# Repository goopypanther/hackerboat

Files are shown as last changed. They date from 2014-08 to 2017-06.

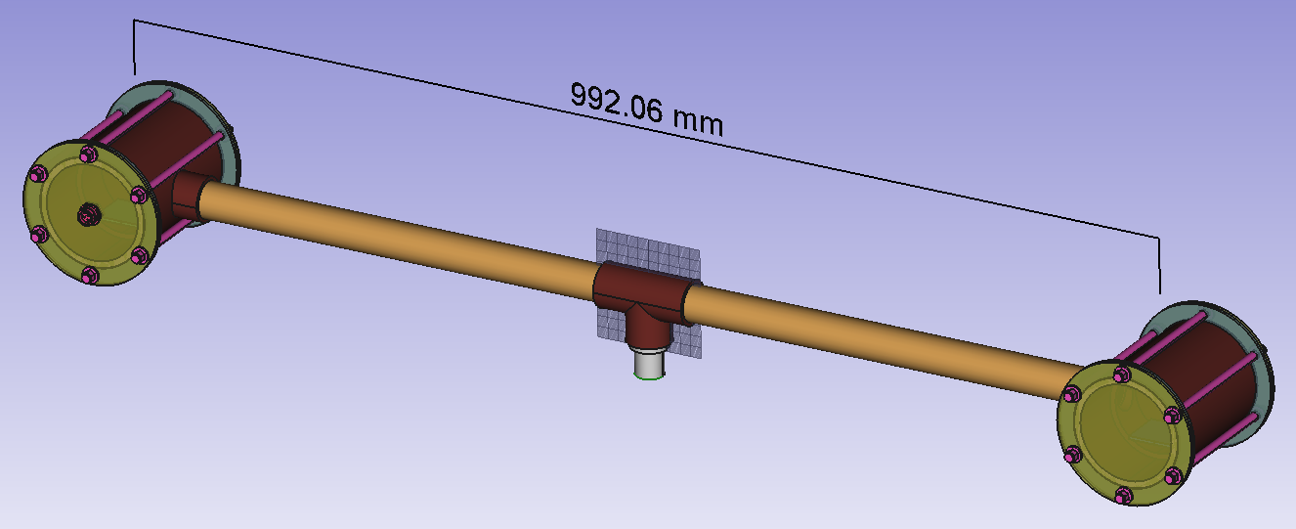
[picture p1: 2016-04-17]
hardware/mounting/StereoEyes/stereo_eyes_finished_model.png

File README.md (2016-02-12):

Hackerboat Control Software
===========================
The hackerbot labs autonomous hackerboat is a modified kayak with 900MHz/2.4GHz radios, electric motor, IMU, scientific sensors & solar power rechargeable batteries.

The control system uses a beaglebone & arduino mega which communicate using REST with a land based host computer.

Embedded Software
-----------------

 * Beaglebone
  * REST communication with host PC
  * IMU/GPS tracking & waypoint navigation
  * MAVLink-over-UART communication with arduino
 * Arduino
  * Motor control
  * Magnetic navigation
  * Ship health & sensor feedback

See [./embedded_software](https://github.com/JeremyRuhland/hackerboat/tree/master/embedded_software)

Doxygen documentation of beaglebone software may be generated with `make doxy` in the `./embedded_software/beaglebone` folder and found at `./embedded_software/beaglebone/doc`.

Host Software
-------------
Javascript served by the Beaglebone. Coming soon...

Hardware Schematics
-------------------
On-ship hardware for connecting beaglebone, arduino and power systems together.

See [./hardware](https://github.com/JeremyRuhland/hackerboat/tree/master/hardware)

Boat System Documentation
-------------------------
View under [./doc](https://github.com/JeremyRuhland/hackerboat/tree/master/doc)

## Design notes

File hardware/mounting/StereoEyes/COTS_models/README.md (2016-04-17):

COTS Models
===========

Sources and descriptions for models downloaded off the web.

4880K583
--------

3in/1in/3in reducing T-joint, female on all sides. Downloaded from mcMaster.

Source: http://www.mcmaster.com/mv1459975500/#4880K583

4880k43
-------

1in T-joint, female. Downloaded from mcMaster.

Source: http://www.mcmaster.com/#plastic-pipe-fittings/=11y0kxh

sp1312_panel_mount_connector
----------------------------

Panel mount connector. Emailed by www.in2connect.uk.com

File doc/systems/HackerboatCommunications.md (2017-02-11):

# Hackerboat Long Range Communications #

## Motivation ##

The previous communications mechanism for the Hackerboat required the boat to run a server to serve the control interface to the control computer. This is not possible given the limitations of most cellular and satellite communications providers, where all connections are initiated by the end user, in this case the boat. 

There are therefore three roles -- the user, who issues commands to the boat, the boat itself, and the intermediate server, which stores and forwards data in both directions. The server receives commands from the user and relays them to the boat when the boat next connects. It receives data from the boat and presents it to the user the next time the user connects. 

## User Communications ##

The communication with the user must allow the user to send commands and see the data returned from the boat. Specification beyond that is not in the scope of this document. 

## Structure of a Boat Communication ##

The boat SHALL begin each communication by issuing an HTTPS POST request to the appropriate end point. The body of the request SHALL consist of a JSON object containing, at minimum, the following fields:

    {BoatName:"<name\>", 
	 BoatKey:<id\>}

Where BoatName SHALL be a unique identifier for the boat and BoatKey SHALL be a 256-bit secret key generated and stored by the server. Unless the BoatName and BoatKey match corresponding values stored in a single record by the server, the server MUST NOT respond to the request. 

If the BoatName and BoatKey match, the server SHALL respond to the command as determined by the contents of the body of the POST and the endpoint to which it is addressed. 

The server SHALL provide the following endpoints:

	<server name>/boat
	<server name>/kml
	<server name>/ais

## <server name\>/boat ##

A valid communication to this endpoint SHALL contain the following fields:

	{BoatName:"<name>",
     BoatKey:<boat key>,
	 Mode:"<boat mode>",
	 NavMode:"<nav mode>",
	 RCmode:"<rc mode>",
	 FaultString:"<faults>",
	 Pose:{timestamp:<decimal seconds>,
		   location:{latitude:<lat>,
					 longitude:<long>},
		   orientation:{heading:<heading>,
						pitch:<pitch>,
						roll:<roll>},
		   GPSheading:<true heading>,
		   GroundSpeed:<GPS speed>
		  },
	}

The variables are defined as follows:

- **BoatName:** The name of the boat, type std::string
- **BoatKey:** A 256-bit secret key shared by the boat and the server.
- **Mode:** The current mode of the boat.
- **NavMode:** The current mode of the navigation subsystem.
- **RCmode:** The current mode of the RC subsystem.
- **FaultString:** A string containing all the current faults.
- **Pose:** The current location and orientation of the boat. 
	- **timestamp** The time at which this data was taken. 
	- **location:** The current position of the boat.
		- **latitude:** The current latitude of the boat, in decimal degrees north.
		- **longitude:** The current longitude of the boat, in decimal degrees east.
	- **orientation:** 
		- **heading:** The current heading of the boat, in degrees clockwise from magnetic north.
		- **pitch:** The current pitch angle of the boat, in degrees from horizontal.
		- **roll:** The current roll angle of the boat, in degrees from horizontal.
	- **GPSheading:** The current course made good, in degrees clockwise from true north.
	- **GroundSpeed:** The speed over the ground, in knots.

The communication MAY also contain the following fields:

	{TargetWaypoint:<waypoint number>,
	 TargetHeading:<target heading>,
	 BatteryData:{timestamp:<decimal seconds>,
		   		  MainBatV:<main battery voltage>,
				  MainBatI:<main battery current>,
				  ChargeV:<charge voltage>,
				  ChargeI:<charge current>,
				  MotorV:<motor voltage>,
				  MotorI:<motor current>,
				  BatMon:<battery monitor>},
	 OutputState:{timestamp:<decimal seconds>,
		   		  RudderPosn:<rudder position>,
				  RudderEnb:<rudder enable>,
				  MotorRelayOutputs:<motor relay bit string>,
				  HornRelay:<horn relay>,
				  StopRelay:<stop relay>,
				  EnbRelay:<enable relay>},
	 HealthMon:{timestamp:<decimal seconds>,
		   		MotorRelayFault:<motor relay fault bit string>,
				HornRelayFault:<horn relay fault>,
				StopRelayFault:<stop relay fault>,
				EnbRelayFault:<enable relay fault>,
				MotorRelay0I:<motor relay 0 current>,
				MotorRelay1I:<motor relay 1 current>,
				MotorRelay2I:<motor relay 2 current>,
				MotorRelay3I:<motor relay 3 current>,
				MotorRelay4I:<motor relay 4 current>,
				MotorRelay5I:<motor relay 5 current>,
				HornRelayI:<horn relay current>,
				StopRelayI:<stop relay current>,
				EnbRelayI:<enable relay current>,
				ServoI:<servo power current>},

	 LinkRSSI:<rssi>,
	 RudderPID:{Kp:<Kp>,Ki:<Ki>,Kd:<Kd>} 
	}

The variables are defined as follows:

- **TargetWaypoint:** The target waypoint, counting the coordinate tuples from zero.
- **TargetHeading:** The target heading, in degress clockwise from magnetic north. 
- **BatteryData:** Data on the various main bus voltages and currents.
	- **timestamp** The time at which this data was taken. 
- **OutputState:** The state of all outputs.
	- **timestamp** The time at which this data was taken. 
	- **RudderPosn:** Rudder position, in microseconds.
	- **RudderEnb:** Rudder enable signal, boolean.
	- **MotorRelayOutpus:** A bit string representing the state of all motor relay outputs.
	- **HornRelay:**
	- **StopRelay:**
	- **EnbRelay:**
- **HealthMon:** State of the various relay outputs and servo current
	- **timestamp** The time at which this data was taken. 
	- **MotorRelayFault:** A bit string representing the faults for each of the motor relay channels. 1 is a fault, 0 is no fault.
	- **HornRelayFault:** This is a boolean; true is faulted.
	- **StopRelayFault:** This is a boolean; true is faulted.
	- **EnbRelayFault:** This is a boolean; true is faulted.
	- **MotorRelay0I:** The current flowing through motor relay 0, in amps.
	- **MotorRelay1I:** The current flowing through motor relay 1, in amps.
	- **MotorRelay2I:** The current flowing through motor relay 2, in amps.
	- **MotorRelay3I:** The current flowing through motor relay 3, in amps.
	- **MotorRelay4I:** The current flowing through motor relay 4, in amps.
	- **MotorRelay5I:** The current flowing through motor relay 5, in amps.
- **LinkRSSI:** RSSI of the network link.
- **RudderPID:** PID constants for rudder control

The response from the server to the boat SHALL contain the following fields:

	{BoatName:"<name>",
	 ServerKey:<server key>,
	 Command:[{Command:<command>,
			   Argument:{<arg object>}},
						  .
						  .
			  . . . . .]}

There MAY be any number of commands, and the boat SHALL execute them in the order presented, from first to last. The list of commands and their arguments is as follows:

	SetMode(mode)
	SetNavMode(nav mode)
	SetAutoMode(auto mode)
	SetHome(optional: location)
	ReverseShell(optional: endpoint)
	SetWaypoint(number)
	SetWaypointAction(action)
	DumpPathKML
	DumpWaypointKML
	DumpObstacleKML
	DumpAIS
	FetchWaypoints(optional: repository)
	PushPath(optional: repository)
	SetPID(Kp, Ki, Kd)

See Commands section, below, for details. 

## <server name\>/kml/<target file\>.kml ##

This endpoint SHALL serve one of the following three [KML](https://developers.google.com/kml/) files:

- waypoints.kml
- obstacle.kml
- path.kml

The waypoints.kml file SHALL contain a single Placemark object that SHALL be named WAYPOINTS and SHALL contain a single LineString object that SHALL contain the waypoints, in order. All references to waypoints SHALL be ordinal numbers referring to this file. 

The obstacle.kml file SHALL contain a polygon for every known obstacle and exclusion zone in the predicted operational area of the vessel.

The path.kml file SHALL contain an individual timestamped Placemark object for every time the boat checks in with the shore server, or as often as directed by compilation variables within the software.

This endpoint SHALL also accept file uploads of these three files with a POST request containing a JSON object of the following format:

	{BoatName:"<name>",
     BoatKey:<boat key>, 
	 <file name>:<file contents>}

Upon receiving such a request, the server SHALL add a timestamp to the filename and store it for inspection.

## <server name\>/ais ##

This endpoint SHALL accept a JSON object of the following format, and store it locally with an attached timestamp.

	{BoatName:"<name>",
     BoatKey:<boat key>, 
	 timestamp:<decimal seconds>,
	 location:{latitude:<lat>,
			   longitude:<long>}
	 AIS:<AIS data>}

Where <AIS data\> is the current database of AIS targets in an array of JSON objects. 

## Commands ##

### SetMode(mode) ###

Set the boat mode to mode. Format of argument SHALL be {mode:"<mode name\>"}.

### SetNavMode(nav_mode) ###

Set the nav system mode to one of:

	IDLE
	AUTONOMOUS

Format of argument shall be {mode:"<mode name\>"}

### SetAutoMode(auto_mode) ###

Set the nav system autonomous mode to one of:

	ANCHOR
	RTLS
	WAYPOINT

Format of argument shall be {mode:"<mode name\>"}

### SetHome(optional: location) ###

Set the boat's home point to either its current location or the optional location argument. Format of argument, if present, SHALL be {home:{latitude:<lat\>,longitude:<long\>}}.

### ReverseShell(optional: endpoint) ###

Open a reverse shell to the given endpoint. If present, the argument SHALL be of the form {endpoint:"<url\>"}.

### SetWaypoint(number) ###

Set the target waypoint to the ordinal number. Argument format SHALL be {waypoint:<number\>}.

### SetWaypointAction(action) ###

Set the action at the end of the waypoint list to one of:

	IDLE
	ANCHOR
	RETURN
	REPEAT

Argument format SHALL be {action:"<action name\>"}

### DumpPathKML(optional: endpoint) ###

### DumpWaypointKML(optional: endpoint) ###
### DumpObstacleKML(optional: endpoint) ###
### DumpAIS(optional: endpoint) ###
### PullWaypoints(optional: repository, key) ###

Fetch waypoints.kml from github using internally stored repository and API key. A new respository and key MAY be specified with the argument format {repository:"<url\>",key:<API key\>.

### PushPath(optional: repository, key) ###

Push current path.kml to github using internally stored repository and API key. A new respository and key MAY be specified with the argument format {repository:"<url\>",key:<API key\>}.

### GetPID ###

Get the current steering PID constant values.

### SetPID(Kp, Ki, Kd) ###

Set the current steering PID constants. Argument format SHALL be {Kp:<kp\>,Ki:<ki\>,Kd:<kd\>}. Omitted values SHALL be left unchanged.

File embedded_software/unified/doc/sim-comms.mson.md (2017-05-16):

# SimOutput (object)
This is the object that the simulation shim writes to the output file. 
Each object is output on a single line -- no pretty printing!

## Properties
- ThrottlePosition (number, required)
	This is the throttle position, and it ranges from -5 to 5
- RudderPosition (number, required)
	This is the rudder position, and it ranges from -100 to 100

# SimInput (object)
This is the object that the simulation shim reads from the input file. 
Each object is output on a single line -- no pretty printing!

## Properties
- GPSposition (object, required)
	- lat (number, required)
	- lon (number, required)
- One Of 
	- HeadingTrue (number)
	- HeadingMag (number)

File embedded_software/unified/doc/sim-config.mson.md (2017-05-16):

# Ladon Sim Configuration (object)
This is the top level configuration for the configuration of the Project 
Ladon simulator shim.

## Properties
- Version (object, required)
	This gives the version of the sim configuration this is written in.
	- Major (number, required)
	- Minor (number, required)
	- Patch (number)
- SimType (enum, required)
	This defines whether the sim is run internally or connects to an 
	external sim runner. 
	- internal (string)
	- external (string)
- InputFile (string)
	The name of the input file to use in external mode. Default is stdin.
- OutputFile (string)
	The name of the output file to use in internal mode. Default is stdout.
- StartPoint (object)
	The GPS location to start the sim at. Used only in internal mode.
	- lat (number, required)
	- lon (number, required)
- CompassError (number)
	This is added to the calculated heading before it is given to the 
	rest of the code. 
- ThrottlePolynomial (number, array)
	Polynomial to map a throttle input into a speed in m/s. Used only for
	internal mode. 
- RudderPolynomial (number, array)
	Polynomial to map a rudder input to a rate of turn in deg/s. Used only
	for internal mode.

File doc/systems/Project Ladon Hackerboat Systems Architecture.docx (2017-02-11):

# Project Ladon Hackerboat Systems Architecture

# 1 Hardware Architecture

The Hackerboat control system is built around a Beaglebone Black, located in a drybox in the forward compartment of the boat. This box contains the Beaglebone, RC receiver, AIS receiver, shore communications transceiver, GNSS receiver, IMU, and associated electronics.

In addition to the main control system box, there is a power distribution box and a motor control box. In the current iteration, the motor control box contains a set of automotive relays that control power to the different windings of the trolling motor.

The power distribution box contains switches and relays to control power distribution to different boat systems. It also contains a latching relay to control the armed status of the boat and maintain it through a power cycle.

## 1.1 Main Board

The main board shall serve as a carrier for the Beaglebone Black as well as core navigation sensors and communications interfaces.

### 1.1.1 Power Input, Conditioning, & Regulation

a) Battery power (12V nominal; 9-20V permitted) shall come in through a 0.375” pitch terminal strip on the top edge of the PCB.
b) The circuit shall be protected by a 3A-5.2A SMD PTC fuse. To protect the circuit from reverse connections, a P-channel MOSFET capable of passing 12A (AO4407A) shall be connected in series with the main power rail with the gate attached to ground. The gate voltage limit of this part (-20V) shall determine the maximum input voltage of the board. This circuit must not pass any current when the power connections are reversed.
c) There shall be a green power status light that is illuminated when the board is powered correctly and a red one illuminated when connected backwards. In addition, there shall be a red fuse status LED that lights when the fuse is open.

#### 1.1.1.1 Battery Monitor

a) The battery monitor circuit shall be directly connected to one of the Beaglebone’s analog inputs.
b) Since these inputs are limited to 0-1.8V, the signal must be passed through a voltage divider and must be further protected by a 1.8V Zener diode to prevent voltage excursions from damaging the circuitry.
c) At 12V nominal input voltage, the expected output of the voltage divider shall be 1.44V.

#### 1.1.1.2 Main 5V Supply

a) The main 5V system supply shall be provided by a V7805-2000 5V/2A switching regulator module. This is designed as a drop-in replacement for the venerable 7805 linear regulators, except with less heat dissipation and much higher efficiency.
b) This power rail shall be connected to the Beaglebone 5V input and the 5V inputs of most onboard peripherals.
c) This power rail shall be available on pins 1-4 of the Accessory Power Connector.

#### 1.1.1.3 Lighting 5V Supply

a) Power for the status lights shall be provided by an identical regulator to the main 5V supply. It is independent to prevent any electrical issues with the lighting from disrupting the main control system.
b) The power rail to the lights shall be protected by a fuse identical to the main power input.

#### 1.1.1.4 Rudder Servo Supply

a) The rudder servo supply shall be independent and set to 7.4V to accommodate the needs of COTS RC servos. It shall be designed to be turned on only when the software and system are in a mode where outputs are active. This is to reduce the possibility of pinch injuries in the exposed reduction gear.
b) Activating the disarm button shall immediately depower the servo supply.
c) To accomplish these aims, the enable line of the 7.4V regulator shall be driven by an AND gate with two inputs – one from a Beaglebone GPIO pin (level shifted as required) and one from the Enable line controlled by the enable/disarm relay on the power distribution board. The Beaglebone connection shall be via a level shifter connected to pin P8.17.
d) A green status LED shall illuminate when the 7.4V supply is active.
e) The output current to the servo shall be monitored by a current shunt resistor and an INA169 high-side current sense amplifier or equivalent connected to the ADC subsystem, chip U19, channel 7. Gain and shunt resistors shall be selected to provide an output of 1.65 V/A.
f) Backup overcurrent protection shall be provided by the saturation limits of the switching supply core.

#### 1.1.1.5 3.3V Supply

a) This supply is provided by the Beaglebone’s internal power regulation circuitry. It is brought out largely to supply the 3.3V rail for the level shifters that allow the Beaglebone’s GPIO pins to interface correctly with 5V input circuitry.
b) This rail shall be provided to external circuitry on pins 7-10 of the Accessory Power Connector.
c) It shall not be protected and must therefore be used with care to prevent disruption to the Beaglebone.
d) Indication of the status of this bus may be provided by the Beaglebone’s own power status light.

#### 1.1.1.6 PoE Supply

a) The main board shall provide a 15V/1A power supply for Ubiquiti PoE devices. This shall be a boost supply that is always on.
b) Overcurrent protection shall be provided by core saturation.

#### 1.1.1.7 Grounding

a) All grounds on the board shall be connected to a common ground plane occupying both sides of the PCB.
b) The corner mounting holes shall be plated through and connected to the common ground plane.

### 1.1.2 Beaglebone Hardware

a) The Beaglebone Black shall be configured with the univ-all cape file in order to provide access to all of the pins for the internal software.

### 1.1.3 IMU

a) The IMU shall be a 9 or 10 DoF unit from Adafruit. Acceptable units include https://www.adafruit.com/products/1604, https://www.adafruit.com/products/1714, and future pin-compatible replacements.
b) The main board shall have mounting holes for a compatible header and the four corner mounting holes.
c) The mounting holes on the PCB shall be grounded.
d) The four corner mounting holes shall be secured to the board with appropriate conductive standoffs.
e) The Vin connection shall be connected to the main 5V rail.
f) The I2C lines shall be connected to the I2C-1 bus on the Beaglebone, using 4.7K pull up resistors. These are 3.3V signals already, so no level shifting is required.
g) The alignment of the IMU relative to the hull of the boat shall be with the X axis pointing forward, the Y axis pointing to port, and the Z axis pointing up.

### 1.1.4 Relay Drivers

The relay driver circuitry groups together power switching and health monitoring circuitry to each relay/solenoid drive channel.

#### 1.1.4.1 General

a) Each relay driver channel shall have a high-side driver with built-in fault, short, and overtemp detection, such as the AUIPS6041G.
b) The input of each switch channel shall be driven with a level shifter from the corresponding 3.3V logic output of the Beaglebone.
c) The fault detection line shall be of an open-drain type, and shall be connected to the 3.3V rail via a pull-up.
d) Each switch input shall be pulled down to prevent unintended activation when the Beaglebone pin is in a high-Z state.
e) Each channel shall have a current monitoring circuit arranged so that the output is 1.65 V/A.
f) Each channel shall have status LEDs indicating both active (green) and fault (red) conditions for each channel
g) Each power output shall have clamp/flyback diodes.

#### 1.1.4.2 Motor Controls

a) Controlling the motor requires driving six automotive relays. These relays shall be numbered 0-5 and connected to a standard 9-pin D-subminiature plug as the output.
b) This connector shall be labeled as Motor Control Relays or similar legend.
c) These lines shall pass out of the main drybox via a seven pin SP-13 connector and enter the motor control box through the existing pair of 4-pin M12 connectors.
d) Assignment of each motor control relay to its end function shall be controlled by software.

Relay Channel | Drive Pin | Fault Pin | ADC Channel
0 | P8.3 | P8.4 | U18, ch 0
1 | P8.5 | P8.6 | U18, ch 1
2 | P8.7 | P8.8 | U18, ch 2
3 | P8.9 | P8.10 | U18, ch 3
4 | P8.11 | P8.12 | U18, ch 4
5 | P8.13 | P8.14 | U18, ch 5

#### 1.1.4.3 Horn

a) One channel shall be dedicated to driving the horn relay, and shall be named as such.
b) It shall use a single 2-pin C-GRID SL connection on the board, running to a 2-pin SP-13 connector in the box.
c) The horn drive relay shall be connected to this connector, and it shall switch main battery power through the horn mechanism.

Relay Channel | Drive Pin | Fault Pin | ADC Channel
Horn | P8.17 | P8.18 | U19, ch 0

#### 1.1.4.4 Enable/Disarm

a) There shall be two relays devoted to switching the enable/disarm latching relay – one to enable and one to disarm.
b) The disarm relay shall allow the Beaglebone software to disarm the boat in response to shore command or conditions other than someone pressing the emergency stop button.
c) The enable relay shall allow the Beaglebone to arm the boat without someone pressing the external go button. This allows the boat to re-arm itself when conditions are right and there are no humans available, as for example in the deep ocean.
d) The arm function shall be arranged so it can be controlled by making or breaking a solder jumper on the board.
e) See the Enable/Disarm Interface, below, for more information on the behavior of these relays.

Relay Channel | Drive Pin | Fault Pin | ADC Channel
Enable | P8.24 | P8.26 | U18, ch 7
Disarm | P8.15 | P8.16 | U18, ch 6

### 1.1.5 R/C Receiver

a) The S-BUS signal from the R/C receiver is serial signal at 100 kbps, 8 data bits, 2 stop bits, and even parity (8e2). It is also inverted relative to the TTL serial standard (i.e. active high rather than the standard active low). The RC receiver also requires power from the 3-pin serial signal connector.
b) The external connectors shall be a pair of 3-pin CGRID SL connectors. Pin 1 shall be ground, Pin 2 shall be +5V, and Pin 3 shall be signal. A power decoupling cap shall be provided.
c) The signal input line shall be protected against voltage and current excursions with a 1K series resistor and a 5V Zener diode to ground.
d) To invert and shift the level from 5V to 3.3V, the signal shall be run through an open drain inverting buffer with the output pulled up to the 3.3V.
e) Due to a shortage of serial interfaces, it shall be possible to connect the R/C receiver via solder jumper to either the GNSS or the Fona Module serial interface. This is acceptable because in the case that the Fona is installed, the GNSS is superfluous. Since the R/C interface is one way, only the receive line may be connected.

### 1.1.6 GNSS

a) The GNSS shall be an Adafruit Ultimate GPS Breakout (https://www.adafruit.com/products/746) or pin-compatible equivalent.
b) The main board shall have mounting holes for a compatible header and the two corner mounting holes.
c) The mounting holes on the PCB shall be grounded.
d) The corner mounting holes shall be secured to the board with appropriate conductive standoffs.
e) The Vin connection shall be connected to the main 5V rail. The RX and TX lines shall be connected to UART4. The Fix pin shall be connected to the Beaglebone at P9.15. The Enable line shall be connected to the Beaglebone at P9.12.
f) No protection or level shifting shall be required.

### 1.1.7 Fona Module

a) The Fona module is an optional ship to shore interface. If installed, it shall be an Adafruit Fona 3G (https://www.adafruit.com/products/3147) or equivalent.
b) The main board shall have mounting holes for a compatible header and the two corner mounting holes.
c) The mounting holes on the PCB shall be grounded.
d) The corner mounting holes shall be secured to the board with appropriate conductive standoffs.
e) The serial interface shall be connected to UART5 and VIO to 3.3V. Other connections shall be as convenient. No level shifting shall be required for this module.
f) Note that this module has been rendered redundant by the 3G cell hotspot described in Ship to Shore Transceiver.

### 1.1.8 ADC subsystem

a) One channel of the Beaglebone’s internal ADC, channel 1, shall be used to sense the Battery Monitor.
b) All other analog inputs shall be via a pair of ADC128D818 8-channel ADCs on a common I2C bus. They shall be powered from the 5V bus to give a 0-5V input range. Doing so requires level shifting the I2C bus; level shifting shall be provided by a single TXS0102 bi-directional level shifter.
c) The I2C lines shall be pulled up to their respective voltages by 4.7K resistors.
d) The 3.3V I2C bus shall be connected to I2C-2.
e) Each input line shall be filtered by an RC filter consisting of a 10K series resistor and a 22 nF parallel capacitor. No protection beyond the filters described above shall be provided for these signals.
f) Channels 1-6 of U19 shall be brought out to the Power Mon connector. This connector shall be a 2x6 0.1” pitch pin header. It is intended to bring in current and voltage sense signals from the motor and charge current/voltage monitors as well as powering those sensors.
g) Three pins shall be connected to +5V and three shall be connected to ground.
h) The other six shall be designated for motor current, motor voltage, charge current, charge voltage, and auxiliary ADC channels 0 and 1.

### 1.1.9 Auxiliary GPIO

a) Eight I/O pins level shifted to 5V shall be provided on the Auxiliary GPIO connector. This shall be a 2x6 0.1” pitch pin header. Two pins shall be +5V and two shall be grounded.
b) Two of the pins shall carry the 5V I2C bus provided for the ADC subsystem. Three shall carry the SPI1 bus, and may optionally be used as GPIOs.
c) The remaining three shall be available as plain GPIOs.
d) In the case of the non-I2C pins, they shall be level shifted through a TXB0108 level shifter. This part shall provide all the available I/O protection to these pins.

### 1.1.10 RS-485

a) The RS-485 interface is intended for future peripheral expansions, including a more advanced motor controller architecture.
b) The RS-485 transceiver chip shall be a half-duplex unit connected to UART1 through one of the onboard TXB0108 level shifters.
c) The direction line shall be similarly level shifted and shall be controlled from pin P9.14.
d) The PCB connector shall be a 3-pin CGRID SL with the following pinout. Pin 1 shall be line B, Pin 2 shall be line A, and Pin 3 shall be ground.

### 1.1.11 Steering

a) The PWM channel for the steering shall be EHRPWM1A on pin P9.16.
b) It shall be level shifted to 5V through one of the onboard TXB0108 level shifters.
c) The 5V output line shall be protected by a 1K series resistor and a 5V Zener diode to ground.
d) The PCB connector shall be a 3-pin CGRID SL with the following pinout. Pin 1 shall be power (7.4V), Pin 2 shall be the PWM output signal, and Pin 3 shall be ground.

### 1.1.12 Lights

a) The exact nature of the lighting interface is still in flux due to difficulties with the interface code.
b) The connector is a 3-pin CGRID SL with Pin 1 connected to the lighting +5V, Pin 2 connected to P9.22 via one of the TXB0108 level shifters, and Pin 3 connected to ground.
c) The signal pin shall be protected with a 1K series resistor and a 5V Zener to ground.

### 1.1.13 Reset

a) The reset line into the Beaglebone is active low, and is provided with a 10K pullup to keep it inactive except as commanded. The external drive is intended to be a hall effect sensor mounted to the interior wall of the drybox, allowing the user to reset the Beaglebone with a small magnet.
b) Therefore, the sensor shall be provided with 5V and ground lines.
c) The signal line shall be high when the hall effect switch is active.
d) The signal shall be run through an inverting buffer and then a level shifter to produce the required active low 3.3V signal at the Beaglebone.
e) The PCB connector shall be a 3-pin CGRID SL with Pin 1 connected to the lighting +5V, Pin 2 connected to the reset line as described above, and Pin 3 connected to ground.
f) The signal pin shall be protected with a 1K series resistor and a 5V Zener to ground.

### 1.1.14 Console

a) The console connector shall bring the receive and transmit lines of the Beaglebone serial console out to a PCB connector.
b) It shall be a 4-pin CGRID SL with Pin 1 NC, Pin 2 connected to RX, Pin 3 connected to TX, and Pin 4 connected to ground.
c) The RX and TX lines shall be protected with a 1K series resistor and a 5V Zener to ground, each.

### 1.1.15 Enable/Disarm Interface

a) The enable/disarm interface provides a connection to the enable/disarm relay in the power distribution box.
b) This interface shall consist of an incoming enable signal, an incoming disarm signal, and outgoing relay drivers for enable and disarm.
c) Each of the two inputs shall be protected by a 1K series resistor and a 5V Zener diode to ground.
d) The enable relay driver shall be connected if and only if solder jumper SJ2 is connected.
e) A high (5V) signal on the enable line shall be required to activate the servo power.
f) Incoming enable and disarm signals shall be level shifted from 5V to 3.3V through one of the onboard TXB0108 level shifters.
g) The enable input to the Beaglebone shall be on pin P8.20 and the disarm input shall be on pin P8.22.
h) The PCB connector shall be a 5-pin CGRID SL. Pin 1 shall be connected to the input enable signal, Pin 2 to the input disarm signal, Pin 3 to ground, Pin 4 to the disarm relay output, and Pin 5 to the enable relay output.

### 1.1.16 PoE Interface

a) The PoE interface shall consist of a pair of unshielded RJ45 connectors back to back. The LAN connector is intended to connect directly to the Beaglebone. The Device connector is intended to be connected to the Ubiquiti gear.
b) Pins 1-3 and 6 shall be directly connected between the two connectors.
c) Pins 4 and 5 on the Device connector shall be connected to the +15V PoE rail. The corresponding pins on the LAN side shall be unconnected.
d) Pins 7 and 8 of the Device connector shall be grounded. The corresponding pins on the LAN side shall be unconnected.

## 1.2 Main Drybox Peripherals

The main drybox has room for several peripherals above and beyond the main board. The ones intended for current or near future installation but not previously discussed are described here.

### 1.2.1 AIS Receiver

a) The AIS receiver shall be a dAISy unit. It shall be connected and powered through the Beaglebone’s USB host port (and optionally, a USB hub).
b) The antenna connection shall be a bulkhead BNC in the outside of the drybox.
c) The antenna shall be mounted as high as practicable.

### 1.2.2 WiFi

a) There shall be two WiFi options – USB dongle and Ubiquiti. One and only one shall be installed.

#### 1.2.2.1 USB Dongle

a) A standard USB WiFi dongle may be used to provide WiFi connectivity. If used with the AIS, it shall be plugged into an appropriate USB hub.

#### 1.2.2.2 Ubiquiti

a) A Ubquiti Nanostation may be used to provide WiFi connectivity.
b) If used, it shall be powered through the PoE interface and plugged from there into the Beaglebone.

### 1.2.3 Ship to Shore Transceiver

a) The ship to shore transceiver shall present a WiFi hotspot that the Beaglebone and any additional equipment may connect to.

#### 1.2.3.1 Current

a) The current ship to shore transceiver shall be a portable 3G cell hot spot. This shall be used for all in-shore work due to its high bandwidth, reliability, and low cost.

#### 1.2.3.2 Future

a) For off-shore work, the ship to shore transceiver shall be an Iridium GO or equivalent system.

## 1.3 Power Distribution Box

The power distribution box provides a common distribution and control point for all power systems on the boat. It also maintains the enable/disarm state through a two-coil latching relay.

### 1.3.1 Board Power

a) At all times when the battery is connected, the power distribution board shall draw power from the power input through a 5V linear regulator.
b) This regulator must be able to handle input voltages from 9VDC to 20VDC.

### 1.3.2 Enable/Disarm Relay

a) The enable/disarm relay shall be a DPDT mechanical relay of the two-coil latching type. The drive for each coil shall be a wire-OR of the relay drive from the main board and a local relay driver activated by either the Enable or Stop button Time Delay Circuits.
b) The enable output signal shall be connected such that when the relay’s SET coil is energized, it will be connected to +12V and to ground when the RESET coil is energized.
c) The disarm output signal shall be wired with the opposite sense.
d) The +12V enable and disarm signals shall be regulated down to +5V with a 1K series resistor and a 5V Zener to ground.
e) The PCB connector for the connection to the main board shall be wired identically to the connector on the main board, as described in Enable/Disarm Interface.

### 1.3.3 Enable and Stop Buttons

a) The Enable and Stop buttons shall be momentary SPDT pushbuttons sealed to IP67 or better and mounted on the outside hull.
b) They shall be given large, obvious actuators – red for stop and green for enable.
c) Both switches shall be wired so that their output signal is normally high.
d) On the PCB, each switch shall be wired to a 3-pin CGRID SL connector. Pin 1 is +5V, Pin 2 is signal, and Pin 3 is ground.
e) The signal pin shall be protected by a 1K series resistor and clamp diodes

### 1.3.4 Time Delay Circuits

a) To prevent inappropriate activation of the Enable and Stop buttons, each shall drive its respective relay coil through a time delay circuit.
b) The time delay circuits shall be one-shots based around the two sides of a 556 dual timer chip. The output of each one-shot and its corresponding input signal shall be NOR’d together to produce an outgoing high pulse after the time delay.
c) These high pulses shall trigger the relay drivers to strobe the corresponding relay coil.
d) The trigger signal for each channel shall be fed forward through an RC low pass network consisting of a 10K resistor and a 1 uF capacitor. This is to ensure that the fed-forward signal remains high until the timer output signal has gone high.

#### 1.3.4.1 Arm Button

a) The delay elements of the arm button shall be a 470K resistor and a 10 uF capacitor, giving a time delay of approximately 5.2 seconds.
b) The input shall be pulled up by a 10K resistor so that if the switch is disconnected, the Arm function will not activate.

#### 1.3.4.2 Stop Button

a) The delay elements of the arm button shall be a 470K resistor and a 2.2 uF capacitor, giving a time delay of approximately 1.1 seconds.
b) The input shall be pulled down by a 1M resistor so that if the switch is disconnected, the Stop function will activate.

### 1.3.5 Switch Controlled Circuits

a) The mechanical switches on the face of the power distribution box shall be SPDT, IP 67 or better, and must be rated for at least 6A and 20VDC.

#### 1.3.5.1 Control Power

a) This switch shall control power to the main drybox.
b) If it is off, power shall not flow to the main drybox.

#### 1.3.5.2 Horn Power

a) This switch shall control power to the horn, allowing it to be turned off during software testing and similar activities.

#### 1.3.5.3 Auxiliary Power 1

a) This switch shall control power to auxiliary power circuit 1.

#### 1.3.5.4 Auxiliary Power 2

a) This switch shall control power to auxiliary power circuit 2.

### 1.3.6 Relay Controlled Circuits

a) Switches for the relay controlled circuits shall switch the coil of an automotive relay rated for at least 30A.

#### 1.3.6.1 Main Power

a) This relay shall control power to all other relays and switches.
b) When it is in the off position, power must not flow to any system other than the power distribution box’s internal circuitry.

#### 1.3.6.2 Motor

a) The motor relay switch shall draw power from the Enable coming from the Enable/Disarm relay.
b) Therefore, if the stop button is pushed, all power flowing to the motor must be cut.

## 1.4 Motor Control Box

The motor control box shall contain seven SPDT automotive relays to switch the four motor wires to control motor direction and speed.

### 1.4.1 Motor Outputs

a) The four motor wires shall be designated by color – red, white, yellow, and black.
b) In forward operation, black shall be connected to ground and the other three lines shall be connected to power and each other in different combinations to produce the five forward speeds.
c) In reverse operation, the polarity shall be flipped.
d) The input power lines shall be +12V (nominal) and ground.
e) A 30A hall effect current and voltage monitor shall be placed in series with the power line and wired back to the main control box.

### 1.4.2 Relay Functions

#### 1.4.2.1 Direction

a) Two relays shall control the direction. Their coils shall be wired in series.
b) Their output sides shall be wired such that when their coils are not energized, +12V (nominal) shall be supplied to the motor box’s positive rail and ground shall be connected to the negative rail.
c) When they are energized, the polarity of the output rails shall be flipped.

#### 1.4.2.2 Red

a) When energized, this relay shall connect the red output to the motor box’s positive rail.
b) When not energized, it shall have no effect.

#### 1.4.2.3 White

a) When energized, this relay shall connect the white output to the motor box’s positive rail.
b) When not energized, it shall have no effect.

#### 1.4.2.4 Yellow

a) When energized, this relay shall connect the yellow output to the motor box’s positive rail.
b) When not energized, it shall have no effect.

#### 1.4.2.5 Yellow-White

a) When energized, this relay shall connect the yellow output to the white output.
b) When not energized, it shall have no effect.

#### 1.4.2.6 Red-White

a) When energized, this relay shall connect the red output to the white output.
b) When not energized, it shall have no effect.

### 1.4.3 State Map

Speed | Direction | Red | Yellow | White | Red-White | Yellow-White
F5 | Off | On | On | On | On | On
F4 | Off | Off | On | Off | On | Off
F3 | Off | Off | On | On | Off | Off
F2 | Off | Off | Off | On | Off | On
F1 | Off | Off | Off | On | Off | Off
Stop | Off | Off | Off | Off | Off | Off
R1 | On | Off | Off | On | Off | Off
R2 | On | Off | Off | On | Off | On
R3 | On | Off | On | On | Off | Off
R4 | On | Off | On | Off | On | Off
R5 | On | On | On | On | On | On

# 2 Software Architecture

The onboard software shall be written in C/C++ and shall run on the Beaglebone Black.

## 2.1 Hardware Interfaces

a) The Beaglebone Black provides a great variety of hardware interfaces natively. Therefore, most of the interface circuitry is I/O protection, with a bit of glue logic and some high current drivers. There are also sixteen external ADC channels.

### 2.1.1 Hardware Abstraction Layer

a) The hardware abstraction layer (HAL) shall provide a mechanism for abstracting the physical interfaces such that they can be modified at need without disturbing the rest of the code base.
b) In the case of inputs that are asynchronous with the main thread of execution, the HAL shall spawn a thread to handle the incoming data and store it as appropriate for the consumption of the main code.

#### 2.1.1.1 Orientation

a) Orientation data shall come from the IMU at a rate of approximately 100 Hz. The raw data shall be in the form of three axis accelerations, three axis magnetometer readings, and three axis rotation rates. Data shall be read and processed by an OrientationInput object which encapsulates the hardware interface and reader thread. It shall present the data to the rest of the program as a pointer to its internal Orientation object. The Orientation object will, at minimum, have pitch, roll, and heading members.
b) While a full orientation solution would be nice to have, the only truly critical data coming from the IMU is heading. The pitch, roll, and heading shall be around the north, east, and down axes. Heading shall be measured in clockwise degrees from north. Pitch shall be measured in degrees from horizontal, with nose-up pitch positive. Roll shall be measured in degrees from horizontal, with starboard rail down positive. The pitch and roll shall be calculated as follows:
c) Roll=tan^(-1) ((a_y)/(√(a_x^2 +a_z^2)))
d) Pitch=tan^(-1) ((a_x)/(a_z))
e) These pitch and roll values shall be calculated using the atan2() function to remove angular ambiguity.
f) The heading shall be calculated with the following formula:[^1]
g) Heading=tan^(-1) ((m_y (√(1-(a_x^2 -a_y^2)/(a_x^2 +a_y^2 +a_z^2)))-m_z ((a_y)/(√(a_x^2 +a_y^2 +a_z^2))))/(m_x (1-(a_x^2)/(a_x^2 +a_y^2 +a_z^2))-m_y ((a_x a_y)/(a_x^2 +a_y^2 +a_z^2))-m_z ((a_x)/(√(a_x^2 +a_y^2 +a_z^2)))(√(1-(a_x^2 -a_y^2)/(a_x^2 +a_y^2 +a_z^2)))))
h) Future implementations may use a Madgwick and Mahoney algorithm to determine orientation instead.

#### 2.1.1.2 R/C receiver

a) The RCInput object shall be the interface between program logic and the the incoming serial data. It shall spawn a thread that listens to the incoming serial data, parses it, and stores it locally for later retrieval.
b) The data from the R/C receiver is packed into twenty-five (25) byte frames. The first byte of each frame is always 0x0f. The next 22 bytes (second byte through twenty-third byte) contain input data channels 0 - 15. Each channel is 11 bits wide, and they are close packed with no spacing. Channels 16 and 17 occupy the first two bits of the twenty-fourth byte. The fourth bit of the twenty-fourth byte is the failsafe bit – if it is set, then the R/C receiver is no longer receiving data from the transmitter. The last byte is the end byte, and it is always 0x00.
c) The RCInput object shall store all eighteen channels as a vector of uint16_t ranging between 0 and 2047. It shall be possible for other code to query the value of any desired channel at any time. The values of channels 16 and 17 shall be either 0 or 2047, depending on whether the corresponding bits are cleared or set.
d) The status of the failsafe function shall be stored as a bool and shall be queriable from user code.
e) The RCInput object shall monitors its incoming datastream. If the datastream ceases or becomes corrupted, the RCInput object shall return false in response to the isValid() method. Otherwise, this method shall return true.
f) The RCInput object shall have the following methods to interpret specific channels:
- getThrottle() shall map channel 0 to an int between -5 and 5
- getRudder() shall map channel 3 to a double between -100 and 100
- getMode() shall return FAILSAFE if isFailSafe() returns true. Otherwise, it shall return RUDDER if channel 4 is far below the midpoint, COURSE is it far above, and IDLE if it is near the midpoint. Note that this corresponds to the three-position switch on the controller.
- getCourse() shall map channel 6 to a double between 0 and 360.

#### 2.1.1.3 GNSS & AIS Input

a) Both the GNSS are AIS inputs shall be processed externally by gpsd. This delivered both data streams as a series of JSON messages on a TCP port. The gpsd package provides a command line utility, gpspipe, that connects a given gpsd server instance to the command line. The GPSdInput object shall use gpspipe to receive the data and the pstreams library to manipulate the incoming stream from program code.
b) The GPSdInput object shall have a set of methods to connect, disconnect, set the host and port, and test whether the connection is good. It shall spawn a listener thread to receive GPS and AIS data and expose that data to the rest of the program.
c) As each JSON message is received, the GPSdInput object shall check if it is a GPS or AIS message. It shall then create an object of the appropriate type, and call the parse() method of that object against the incoming message. If it fails, both the new object and the message are discarded.
d) If the incoming message is a GPS message and is successfully parsed, it shall be copied to a private GPSFix object. A pointer to this internal object shall be returned by the getFix() method.
e) If the incoming message is an AIS message, it shall be compared with the internally stored map of AIS contacts. If it has the same MMSI number as an existing contact, the fields of the incoming that are present shall be copied into the existing AIS contact and the last contact time shall be set to the current time.
f) There shall be a method to prune the AIS map for stale contacts and contacts that are too far distant to have an impact on the boat.

#### 2.1.1.4 Rudder (Servo)

a) R/C servos are controlled with a PWM scheme running at between 50 and 100 Hz. The positive pulse is nominally between 1000 and 2000 µsec long but can range from 600 to 2400 µsec. 1500 µsec is the nominal midpoint.
b) The PWM peripheral on the Beaglebone is controlled by writing values to the appropriate values and hooking the peripheral up with the internal pinmux. The appropriate pinmux shall be configured using the config-pin script.
c) The input shall be accepted as either a raw µsec value or as a mapped value from -100 to 100.
d) The Servo object shall handle all interface with the files required to drive the PWM peripheral.

#### 2.1.1.5 Throttle

a) The Throttle object shall drive the motor control relays to translate a given throttle command into the outputs required to get that speed from the motor. See Motor Control Box for more details on the relay functions.

#### 2.1.1.6 Analog Input

a) The ADCInput object shall use a listener thread to read from the battery monitor (internal ADC) and external ADCs at a rate of at least 100 Hz. The resulting data will be available as either raw codes (0-4095) or as scaled values. The channels shall be callable by descriptive names; the relation to physical channels shall be set at object construction from a configuration file.
b) The calling code shall be able to set any number of offsets or gains independently. When a new value is sampled, the scaled value shall be calculated by adding the offset and multiplying by the gain, in that order.

#### 2.1.1.7 GPIO

a) The Pin object shall present an interface to any given GPIO pin. It shall handle the pinmux configuration through the config-pin script and reading/writing the appropriate configuration and value files in /sys/class/gpio/gpio**. The Pin object shall include methods for translating between different representations of the same gpio pin.
b) The Pin object shall be created pointed at a specific pin. The pin shall be defined by the connecter (either 8 or 9) and pin (1-46) on that connector. The object shall contain methods to set the direction (true for output, false for input), writing, and reading the pin. The readPin() method shall return 1 for high, 0 for low, and -1 for any read error. The object shall also contain methods for setting the internal pullup and pulldowns. Changes to pin configuration (direction, pull up/down, etc) shall require a call to the init() method to take effect.

#### 2.1.1.8 Relays

a) The Relay module shall consist of two classes – a Relay class for describing a single relay and a RelayMap singleton for providing access to named relays from program code. The module shall also contain a typedef for a RelayTuple.

##### 2.1.1.8.1 RelayTuple

a) A RelayTuple shall be of type std::tuple<double, bool, bool> where the elements represent the current in amps, the drive state of the relay (true = on), and the fault state of the relay (faulted = true), respectively.

##### 2.1.1.8.2 Relay

a) A Relay object shall encapsulate a name (type std::string), a pointer to a drive Pin, and a pointer to a fault Pin. It shall also contain a pointer to an ADCInput object that contains a channel of the same name as the relay to provide current feedback.
b) The object shall contain methods to turn the target relay on and off, check the current, check for fault states, and return the current state of the relay as a tuple.

##### 2.1.1.8.3 RelayMap

a) The RelayMap singleton shall contain a named map of Relay objects and shall use a hard-coded initializer defined in a system level configuration file. It shall have a function that returns a pointer to the Relay object associated with a given name.

#### 2.1.1.9 Test Harness

a) To ease unit and integration testing of the HAL code and code that depends on it, all HAL classes shall declare HalTestHarness as a friend. This requires a forward declaration of HalTestHarness.
b) Each HAL class that requires test harnessing shall be represented by a method in the test harness class. This method shall provide an interface to extract mutable pointers to each private member of the target class required to provide test functionality.
c) The accessADC() method shall take a pointer to the target ADCInput object, a pointer to a pointer of type map<string, int> to represent the raw values, and a pointer to a pointer of type bool to represent whether the data is valid. The referenced pointers shall be directed to the _raw and inputsValid private members of ADCInput, respectively.
d) The accessGPSd() method shall take a pointer to the target GPSdInput object, a pointer to a pointer of type GPSFix, and a pointer to a pointer of type map<int, AISShip>. The referenced pointers shall be directed to the _lastFix and _aisTargets private members of the given GPSdInput object, respectively.
e) The accessOrientation() method shall take a point to the target OrientationInput object, a pointer to a pointer of type Orientation, and a pointer to a pointer of type bool. The referenced pointers shall be directed to the _current and sensorsValid members of the given OrientationInput object, respectively.
f) The accessRC method shall provide access to the following members of the given RCInput object:
  - _throttle
  - _rudder
  - failsafe
  - _valid
  - rawChannels
  - inbuf
  - _errorFrames
  - _goodFrames
g) The accessRelay() method shall provide access to the drive and fault Pin objects of the given relay.
h) The initGPIOTest() method inverts the OS level direction of the GPIO referred to by the given Pin object and currently set as an input.
i) The writeGPIOTest() method shall write a new value to a Pin set as an input and previously modified with initGPIOTest().
j) The readGPIOTest() method shall read the current value of a Pin set as an output.

### 2.1.2 Ship to Shore Communications

a) From the perspective of the Beaglebone, ship to shore communications shall be over a WiFi link. It must be agnostic to the exact nature of the ship to shore link, so that an Iridium Go may be substituted for a cell hotspot with no code changes.
b) The protocol used shall be MQTT. The default message broker for now shall be Adafruit.io. Connections shall be via SSL if possible.[^2]
c) Payloads may be JSON, CSV, or plain values, as noted per topic. All numeric values shall be double precision floats unless otherwise noted. The MQTT wrapper class shall provide methods to iterate through a list of publisher functions.
d) The MQTT object shall subscribe to the listed subscription topics on startup. Incoming commands shall be pushed to the command queue described in BoatState.

#### 2.1.2.1 Topics Published by the Boat

Topic Name | Format | Data
SpeedLocation | CSV | | <speed, knots>,<lat, degrees>,<lon, degrees>,0
Mode | CSV | | <boat mode>,<nav mode>,<auto mode>,<rc mode>
Bearing | Plain | | Current heading, degrees from magnetic north
BatteryVoltage | Plain | | battery voltage
RudderPostion | Plain | | rudder position, -100 to 100
ThrottlePosition | Plain | | Throttle position, -5 to 5
RudderK | JSON | | {“Kp”:<proportional>,”Ki”:<integral>,”Kd”:<differential>}
Course | Plain | | Course made good, degrees true
Health[^3] | JSON | | Packed JSON of HealthMonitor object

#### 2.1.2.2 Topics Subscribed to by the Boat

Topic Name | Format | Data
Command | JSON | | {“Command”:<function name>,”Arguments”:<args>}

## 2.2 Software Modules

a) This section covers the program logic, both core and supporting.
b) The main program shall run in timed frames at a rate of 50 ms per frame (20 Hz)
c) At the start of each frame, the code shall read all sensors.
d) The code shall then execute the current mode of the state machine.
e) Lastly, the code shall write to any outputs not written by the mode logic.

### 2.2.1 Data Types

#### 2.2.1.1 HackerboatState

a) All the custom datatypes shall be subclasses of the HackerboatState abstract base class. It shall define the following virtual methods:

Method | Arguments | Returns | Description
parse | json_t* | bool; true on success | Populate this object from the given JSON
pack | void | json_t* | Serialize this object into JSON
isValid | void | bool; true if object is valid. | Determine whether the current object is in a valid state.

b) The class shall define a public member recordTime, which shall be a timepoint as defined in the <chrono> library.
c) The class shall define two static utility methods, parseTime() and packTime(). These act as wrappers for the date library and provide a uniform conversion between timepoints and string representations of timestamps.

#### 2.2.1.2 HackerboatStateStorable

a) The HackerboatStorable class shall bn abstracte a subclass of the Hackerboat class that provides a common interface for those datatypes that require database storage and retrieval.
b) The HackerboatStateStorable class shall define a new type, sequence, as an alias of int64_t. This shall be used to store a monotonic sequence number in a protected data member. The sequence number shall increment each time this object is written to the database. There shall be a public method that returns the sequence number.
c) The class shall contain the following non-virtual but overloadable public methods:

Method | Arguments | Returns | Description
countRecords | void | sequence | Returns number of rows in the corresponding database table.
writeRecord | void | bool (true if successful) | Write the contents of the current object to the corresponding database row, if it exists.
getRecord | sequence | bool (true if successful) | Populate the current object with the contents of the database row specified.
getLastRecord | void | bool (true if successful) | Populate the current object with the contents of the most recent row.
appendRecord | void | bool (true if successful) | Append the contents of the current object as the last row in the database.

d) Each subclass must implement a storage() method that returns a handle to the database table corresponding to that subclass in the form of a reference to a HackerboatStateStorage object.
e) Each subclass may implement fillRow() and readFromRow() to write and read rows from the database table associated with this object. If either is implemented, both must be implemented. They shall default to writing and reading the sequence number and a text string containing the JSON representation of the object produced by the pack() method.

#### 2.2.1.3 HackerboatStateStorage

a) A HackerboatStateStorage object shall encapsulate a reference to a table in a SQLite3 database file. It shall further contain prepared statements and methods for implementing all the methods described in HackerboatStateStorable .

#### 2.2.1.4 Enumerations

a) The code shall use enumerations to represent values that can only take a limited number of named values.
b) All enums shall be of the type enum class.

##### 2.2.1.4.1 BoatModeEnum

a) This enumeration shall contain the names of all the top-level modes of the boat. See Control Modes for more detail.

##### 2.2.1.4.2 NavModeEnum

a) This enumeration shall contain the names of all the navigation modes of the boat. See Control Modes for more detail.

##### 2.2.1.4.3 AutoModeEnum

a) This enumeration shall contain the names of all the autonomous modes of the boat. See Control Modes for more detail.

##### 2.2.1.4.4 RCModeEnum

a) This enumeration shall contain the names of all the R/C modes of the boat. See Control Modes for more detail.

##### 2.2.1.4.5 WaypointActionEnum

a) This enumeration shall contain the action that the Waypoint Navigation module takes when it reaches the end of the list of waypoints.

Action Name | Enum Name | Description
Idle | IDLE | Boat stops and does nothing – Navigation mode goes to Idle.
Anchor | ANCHOR | Hold position at the last waypoint.
Return | RETURN | Return to the origin point and hold position once there.
Repeat | REPEAT | Repeat the list of waypoints, starting with the first.
None | NONE | This is effectively the default uninitialized state. Functionally equivalent to Idle.

#### 2.2.1.5 EnumTable

a) To produce human-readable JSON, each enum shall be paired with a vector of strings corresponding to the names of the enum elements.
b) EnumTable shall have a public method which determines whether a given string names an element of the enum.
c) EnumTable shall have public methods allowing the user to get the string given the enum value or the enum value given the string.
d) The string values shall be defined in BoatState.

#### 2.2.1.6 Timestamps

a) Timestamps shall conform to ISO8601 and shall have a precision of milliseconds or better. This shall be accomplished using Howard Hinnant’s date library.

#### 2.2.1.7 BoatState

a) BoatState is intended to be a full log of the status of the boat, and therefore shall store the value of, or pointers to, information about every major subsystem. The intent is that a pointer to it can be passed to each mode object in the State Machine and provide the mode execute() methods with all the hooks required to control the boat.
b) BoatState shall be a subclass of HackerboatStateStorable.
c) BoatState shall maintain a colon separated list of current faults with boat systems. It shall provide methods to add faults, remove faults, clear the fault string, and count the number of entries it contains.
d) BoatState shall maintain a reference to the current state of each layer of the state machine, and shall have public accessors for this data.
e) BoatState shall have a queue for storing incoming commands from the ship to shore link. It shall be able to execute any number of queue elements from a single method call. It shall also have methods for clearing the queue and adding new members.
f) BoatState shall have a method for serializing its data as a CSV string.
g) BoatState shall have a member of type Waypoint that stores the list of waypoints as described in Waypoint Navigation. It shall also store the number of the current waypoint and the action to take when the last waypoint in the list is reached.
h) BoatState shall store the timepoints at which it last received data from the ship to shore link and from the R/C receiver.
i) BoatState shall maintain the location from which it launched.
j) BoatState shall maintain a pointer to the Health Monitoring subsystem.
k) BoatState shall maintain a copy of the last GPS fix.
l) BoatState shall maintain pointers to the Servo, Throttle, RCInput, ADCInput, GPSdInput, OrientationInput, and RelayMap subsystems.
m) BoatState shall maintain Pin objects for the Enable and Disarm inputs.
n) BoatState shall maintain a Pin object for the servo enable pin.

#### 2.2.1.8 Command

a) The Command class is intended as a storage container for commands received on the command topic from the shore side MQTT broker.
b) A Command object shall be built with a pointer to the current BoatState (to allow it to act), the name of the command, and a json_t* pointer to the arguments.
c) The Command class shall have an execute() method that calls the current command. It shall take an argument indicating the number of commands from the queue to execute. It shall return the number of commands successfully executed (i.e. returning true).
d) All commands shall be implemented as private static methods of the Command class.

##### 2.2.1.8.1 SetMode

a) This function shall request the desired boat level mode for the next iteration of the state machine. It is up to the current mode implementation whether this causes the mode to transition or not.
b) The argument JSON object shall consist of a single key named “mode”. The value of mode shall be the string name of the desired mode.

##### 2.2.1.8.2 SetNavMode

c) This function shall request the desired navigation level mode for the next iteration of the state machine. It is up to the current mode implementation whether this causes the mode to transition or not.
a) The argument JSON object shall consist of a single member key “mode”. The value of mode shall be the string name of the desired mode.

##### 2.2.1.8.3 SetAutoMode

d) This function shall request the desired autonomous level mode for the next iteration of the state machine. It is up to the current mode implementation whether this causes the mode to transition or not.
a) The argument JSON object shall consist of a single key named “mode”. The value of mode shall be the string name of the desired mode.

##### 2.2.1.8.4 SetHome

a) If this function is called with no arguments, it sets the home point to the last GPS fix received.
b) This function may be called with the argument “location”. If this key contains the JSON representation of a valid Location object, the home point shall be set to the given location.

##### 2.2.1.8.5 ReverseShell

a) This function shall open a reverse shell connection to allow fine grained control, configuration, and modification of the Beaglebone Black over the ship to shore link.
b) This function has not yet been implemented. Options include SSH over Pagekite and MOSH.

##### 2.2.1.8.6 SetWaypoint

a) This function shall set the target waypoint number.
b) The argument shall be a single key named “number” with the value of the desired waypoint.
c) It shall check to make sure the desired waypoint exists. If it is greater than the number of waypoints, it shall set the target waypoint to the last waypoint. If it is less than zero, it shall set the current waypoint to the first waypoint.

##### 2.2.1.8.7 SetWaypointAction

a) This function shall set the action that the boat takes on reaching the last waypoint in the list.
b) The argument JSON object shall contain a single key, “action”. Its value shall be a string representing one of the possible values of WaypointActionEnum.
c) If the argument does not contain the “action” key or the value of the key is not a valid value of WaypointActionEnum, this function does nothing and returns false.

##### 2.2.1.8.8 DumpPathKML

a) This function shall dump a KML file containing a LineString object describing the course of the boat to date to the given web address.
b) This function is not yet implemented.

##### 2.2.1.8.9 DumpWaypointKML

a) This function shall dump a KML file containing the waypoint list to the given web address.
b) This function is not yet implemented.

##### 2.2.1.8.10 DumpObstacleKML

a) This function shall dump a KML file containing all obstacles known to the boat at the current time to the given web address.
b) This function is not yet implemented.

##### 2.2.1.8.11 DumpAIS

a) This function shall dump a JSON representation of the current AIS database to the given web address.
b) This function is not yet implemented.

##### 2.2.1.8.12 FetchWaypoints

c) This function shall fetch a new waypoint KML file from either a hard-coded default location or the given web address.
d) This function is not yet implemented. This function imposes substantial security risks and must be carefully considered before implementation.

##### 2.2.1.8.13 PushPath

a) This is a duplicate of DumpPathKML and should be deleted.

##### 2.2.1.8.14 SetPID

a) This function allows remote setting the rudder PID proportional, integral, and differential gains.
b) The argument JSON object may contain any combination of the keys “Kp”, “Ki”, and “Kd”, representing the proportional, integral, and differential gains, respectively.
c) The value of these keys shall be interpreted as double precision floating point numbers and written to the appropriate location in the BoatState object passed to this function.

#### 2.2.1.9 HealthMonitor

a) The HealthMonitor class is intended to bring all vehicle health monitoring data into a single object, easing data acquisition, scanning, and logging.
b) HealthMonitor shall be a subclass of HackerboatStateStorable.
c) The object shall maintain a pointer to an ADCInput object used to read the incoming sensors.
d) It shall implement a single function readHealth() that populates the object with the system health data from around the boat.
e) The object shall gather and store the following vehicle health data:
  a. Servo current
  b. Battery Voltage (measured at control board)
  c. Main Battery Voltage
  d. Main Battery Current
  e. Charge Voltage
  f. Charge Current
  g. Motor Voltage
  h. Motor Current
  i. R/C RSSI value
  j. Cellular/Satellite RSSI value
  k. WiFi RSSI value

#### 2.2.1.10 AIS

a) AIS data shall be received from gpsd as described in GNSS & AIS Input.
b) AIS data shall be in the format described in http://catb.org/gpsd/gpsd_json.html and http://catb.org/gpsd/AIVDM.html

##### 2.2.1.10.1 AIS Enums

a) This module shall contain enumerations to describe the Message Type, Navigation Status, Ship Type, and EPFD Type fields described in http://catb.org/gpsd/AIVDM.html.

##### 2.2.1.10.2 AISBase

a) The AIS module shall contain an abstract base class, AISBase. All AIS contact types shall be subclasses of this base class.
b) AISShip shall be a subclass of HackerboatStateStorable.
c) AISBase shall contain a virtual prune() method that, upon calling determine whether the current AIS object ought to be removed from the database.
d) AISBase shall have an MMSI member to store the contact’s identity.
e) AISBase shall contain a member storing the last time at which an AIS message was received from this contact.
f) AISBase shall contain a member storing the last reported location of the contact.

##### 2.2.1.10.3 AISShip

a) AISShip shall contain a method for parsing the JSON packet delivered by gpsd.
b) AISShip shall be a subclass of AISBase.
c) AISShip shall contain a project() method that estimates the current location of the contact either now or at some timepoint in the future.
d) AISShip shall contain a merge() method that allows two AISShip objects with the same MMSI to be merged. The most recent data will be used when both contain valid values for a member.
e) AISShip shall contain the following public members:

Name | Type | Description
status | AISNavStatus | The navigation status of the vessel
shiptype | AISShipType | The type of vessel
epfd | AISEPFDType | The type of EPFD mounted by the vessel
turn | double | Rate of turn of the vessel in degrees per min
speed | double | Speed of vessel in knots
course | double | True course of vessel in degrees from true north.
heading | double | Magnetic heading of vessel in degrees from magnetic north.
callsign | string | Callsign of vessel
shipname | string | Name of vessel
imo | int | IMO number of vessel
to_bow | int | Distance from the GNSS antenna to the bow in meters
to_stern | int | Distance from the GNSS antenna to the stern in meters
to_port | int | Distance from the GNSS antenna to the port rail in meters
to_starboard | int | Distance from the GNSS antenna to the starboard rail in meters

f) The prune() function shall recommend removal of this contact when any of the following conditions are met:
  a. No signal from the contact has been received in AIS_MAX_TIME (defined in config.h)
  b. The contact is farther away than AIS_MAX_DISTANCE (defined in config.h)
g) When called, the prune() function shall remove the corresponding row from the database.

#### 2.2.1.11 GPS

a) The GPSFix class shall store the details of each incoming GPS fix from gpsd.
b) GPSFix shall be a subclass of HackerboatStateStorable.
c) GPSFix shall implement a method for parsing the JSON received from gpsd as described in GNSS & AIS Input.
d) The header file containing GPSFix shall contain an enum class called NMEAModeEnum that encodes the fix mode provided with each GPS report from gpsd. Possible values are NONE, NOFIX, FIX2D, and FIX3D.
e) GPSFix shall maintain the following public data members:

Name | Type | Description
fix | Location | The location of the current fix
gpsTime | sysclock | The GPS time of the current fix
mode | NMEAModeEnum | The mode of the current fix
device | string | Name of the source device (may be excluded if desired)
track | double | Course over ground, in degrees from true north
speed | double | Speed over ground, in m/s
alt | double | Altitude above MSL, in meters
climb | double | Rate of climb in m/s.
epx | double | Longitude error in meters, 95% confidence
epy | double | Latitude error in meters, 95% confidence
epd | double | Course error in degrees, 95% confidence
eps | double | Speed error in m/s, 95% confidence
ept | double | Timestamp error in second, 95% confidence
epv | double | Altitude error in meters, 95% confidence
epc | double | Climb error in m/s, 95% confidence
fixValid | bool | True if this is a valid fix

#### 2.2.1.12 Orientation

a) The Orientation class shall store the current pitch, heading, and roll of the boat.
b) The Orientation class shall be a subclass of HackerboatState.
c) The Orientation class shall be aware of the difference between true and magnetic headings, and shall have methods to convert between the two.
d) It shall use GeographicLib to calculate magnetic declination. Declination shall be recalculated only on request, because it is time consuming to do so.
e) It shall store pitch, roll, and heading as public data members of type double.
f) Pitch, roll, and heading shall default to NAN.

#### 2.2.1.13 Location

a) The Location class shall provide a mechanism for storing and working with geographic locations.
b) The Location class shall be a subclass of HackerboatState.
c) The Location class shall store lat and lon as public data members of type double.
d) The header containing the Location class shall define CourseTypeEnum, which shall have the possible values of GreatCircle and RhumbLine.
e) All Location methods that calculate geographic relationships shall take a CourseTypeEnum as an argument, with the default value of GreatCircle.
f) All such methods will use GeographicLib to calculate courses and distances.
g) The Location class shall define a method bearing() which calculates the true bearing from the calling Location object to another given Location object.
h) The Location class shall define a method distance() which calculates the distance from the calling Location object to another given Location object.
i) The Location class shall define a method target() which returns a TwoVector with units of meters that transforms the calling Location to the given Location object.
j) The Location class shall define a method project() which adds a given TwoVector to the calling Location and returns a new Location object.

#### 2.2.1.14 Utility Types

##### 2.2.1.14.1 TwoVector

a) The TwoVector class shall store a two-dimensional vector.
b) All TwoVector methods shall be declared inline.
c) The TwoVector class shall implement access methods for both Cartesian and polar representations.
d) The TwoVector class shall provide rotation methods for both degree and radian input.
e) The TwoVector class shall provide scalar multiplication and division operators.
f) The TwoVector class shall provide vector addition and subtraction operators.
g) The TwoVector class shall provide the dot product as a multiplication operator.
h) The TwoVector class shall provide a unit() method which returns the unit vector.
i) The TwoVector class shall provide rad2deg() and deg2rad() static methods for angle conversions.

### 2.2.2 Logs

The current logging code is clunky to use and doesn’t provide much in the way of protection against race conditions and the like. It is documented here for historical interest and to facilitate writing code until it is replaced.

#### 2.2.2.1 Current

a) The logging class, LogError, shall be a singleton.
b) It shall implement an open() method which opens a given log file for writing.
c) The write() method shall take two arguments, a source and a message. The source argument shall name the origin of the error message and the message argument shall contain the text.
d) The write() method shall write a millisecond resolution timestamp in square brackets, followed by the source, a colon, and the message.
e) The close() method shall close the log file. Since this is a singleton and there is only one ofstream, this must be called immediately to prevent race conditions.

#### 2.2.2.2 Planned

a) Logging shall be handled the EasyLogging++ library (https://github.com/easylogging/easyloggingpp)
b) Time format shall be [%Y-%M-%d-%H:%m:%s.%g], for example: [2016-11-03-20:12:22.136]
c) Each module may have its own custom logger in addition to the main logging facility.

### 2.2.3 State Machine

a) The core of the software is a multi-layer state machine. Each layer has a base class that instantiates the StateMachineBase template. Each mode[^4] in that layer is a subclass of the layer’s base class. The template requires each mode to implement an execute() method. This method contains all logic for the given mode.
b) The execute() method returns a pointer to an object that is a subclass of its layer’s base class. To execute a step of the state machine, the code shall call the execute() method of the mode object that the current state machine pointer points at. It shall then replace the current state machine pointer with the new pointer returned from the call to the current mode’s execute() method.
c) The Navigation mode shall have an RC Command mode pointer and an Autonomous mode pointer as members.
d) Each layer’s base class shall implement a factory() method that returns a pointer to a new mode object of the desired mode type.
e) See Control Modes for a full description of all available modes.

### 2.2.4 Waypoint

a) The Waypoint class loads waypoints in from an external KML file, keeps track of the current waypoint, and provides that waypoint as a Location object on request.
b) The Waypoint object shall, on command, load an external KML file. It shall search for a <Placemark> named “Waypoints”, and search within that <Placemark> for a <LineString>. If it finds an appropriate <LineString>, it will load the latitude and longitude points from the <coordinates> field, in order.
c) Loading a KML file shall overwrite the existing waypoint list if and only if it contains at least one valid coordinate.
d) The Waypoint class shall define appropriate methods for accessing and manipulating the locations of the waypoints and the current waypoint number.
e) Determining and steering the course to the next waypoint shall be handled by the appropriate modes’ execute() method(s).

### 2.2.5 Obstacle Avoidance

There are two schemes here for obstacle avoidance – a stateless scheme designed to avoid pop-up obstacles, such as might be detected by cameras and a stateful scheme based on the A* algorithm to dodge fixed obstacles, such as coastlines and AIS contacts. In the future, the stateful scheme can also be used for wind finding by a sailing version of the boat.

#### 2.2.5.1 Vector Summation[^5]

a) The primary vector shall be the one pointed at the next waypoint. Its length shall be determined by the value of the WaypointStrength member of the BoatState object. All other navigation vectors shall be summed with it to determine the actual course.
b) If the A* system is active, the active waypoint shall be the direction to the next intermediate waypoint as determined by the A* algorithm.
c) The dodge code shall execute the following procedure for all known obstacle points, starting from one side of the obstacle detection field.
  a. Determine the bearing to the obstacle point.
  b. Determine if this obstacle point is within a given distance[^6] of the last obstacle point.
  c. If yes, add a vector perpendicular to the obstacle’s bearing, pointing in the same general direction as the last vector,[^7] and with a length proportional[^8] to the distance to the obstacle.
  d. If no, add a vector perpendicular to the obstacle’s bearing, pointing in towards the primary vector, and with a length proportional to the distance to the obstacle.[^9]
d) A noise term shall be added to the vector in order to prevent deadlock.
e) The vector calculated in paragraph (c) shall be summed with the primary vector to produce a target course.

#### 2.2.5.2 A*

a) The A* algorithm shall take as input data current location, destination waypoint, an appropriate representation of those areas where the boat is not allowed,[^10] and the current AIS database.
b) The neighbors of any given point for the purposes of this algorithm shall be that set of points that can be reached by traveling for a given time step under current or predicted weather conditions. If the destination waypoint is within this locus of points, it shall be a neighbor.
c) g(n) is the number of segments in the path.
d) h(n) is the distance from the point under consideration to the destination waypoint divided by the average length of each segment to this point. This scaling factor is to make the values of g(n) and h(n) directly comparable.
e) The cost of a point that lies within a forbidden area or the exclusion zone around the predicted position of an AIS contact shall be infinite.
f) The A* algorithm shall proceed until either:
  a. The elapsed time is longer than the pathfinding time horizon.
  b. One or more paths reach the target waypoint.[^11]
g) The A* algorithm shall maintain its list of intermediate waypoints until the next time it is computed.

### 2.2.6 PID Control

a) The primary use of PID control is to drive the rudder, but the logic is available for other purposes if required.
b) On construction, the PID object shall be passed pointers to input, output, and setpoint, which are all of type double.
c) The error term shall be the value of the setpoint minus the value of the input at the time of calculation.[^12]
d) The integral term is a running sum of the error term, bounded by the output limits stored within the PID object.
e) The differential term is the difference between the current input and the last input.
f) The output shall be calculated with this formula: output=K_p *error+ K_i *integralTerm-K_d *(input-lastInput)
g) The PID object shall be settable for either a direct or reverse process, i.e. negative or positive response to a positive input, respectively.
h) The PID object shall have two modes – automatic and manual. In manual mode, the PID loop is calculated every time the Compute() method is called. In automatic, it calculates when Compute() is called if and only if the specified sample time has passed since the last time it calculated.
i) The PID constants shall be interpreted as being in terms of whole seconds. This means that the integral terms shall be divided by the frequency (in Hertz) and the differential term shall be multiplied by the frequency.
j) The PID constant shall store and return the initially entered values of the constants when queried.

### 2.2.7 Database Storage

#### 2.2.7.1 HackerboatStateStorage

a) Database interactions will be handled through the HackerboatStateStorage class.
b) Storage will be in SQLite3 database files
c) A static databaseConnection() method shall store the names of all open database files and provide shared handles for each open file.
d) The constructor shall take an initializer list of struct type column.
e) The column struct shall be defined locally and shall consist of two const char* strings, name and type. These shall be used to drive the createTable() method.
f) The createTable() method shall be used to create the table referred to by the current object if it does not already exist.
g) The HackerboatStateStorage class shall provide methods that return shared statement references for querying, inserting, and updating records.

#### 2.2.7.2 SQLiteParameterSlice

a) SQLiteParameterSlice shall encapsulate an interface to prepare a database row for insertion or appending to the table referred to in the shared statement that it is constructed with.
b) It shall define bind() methods for double, int, int64_t, bool, std::string, and JSON values.

#### 2.2.7.3 SQLiteRowReference

a) SQLiteRowReference shall encapsulate and interface to read data in from a given database row returned by the shared statement it is constructed with.
b) It shall define a <type>_field() method to read each of the types that SQLiteParameterSlice can write.

## 2.3 Control Modes

a) The control modes encapsulate the mission logic of the boat.

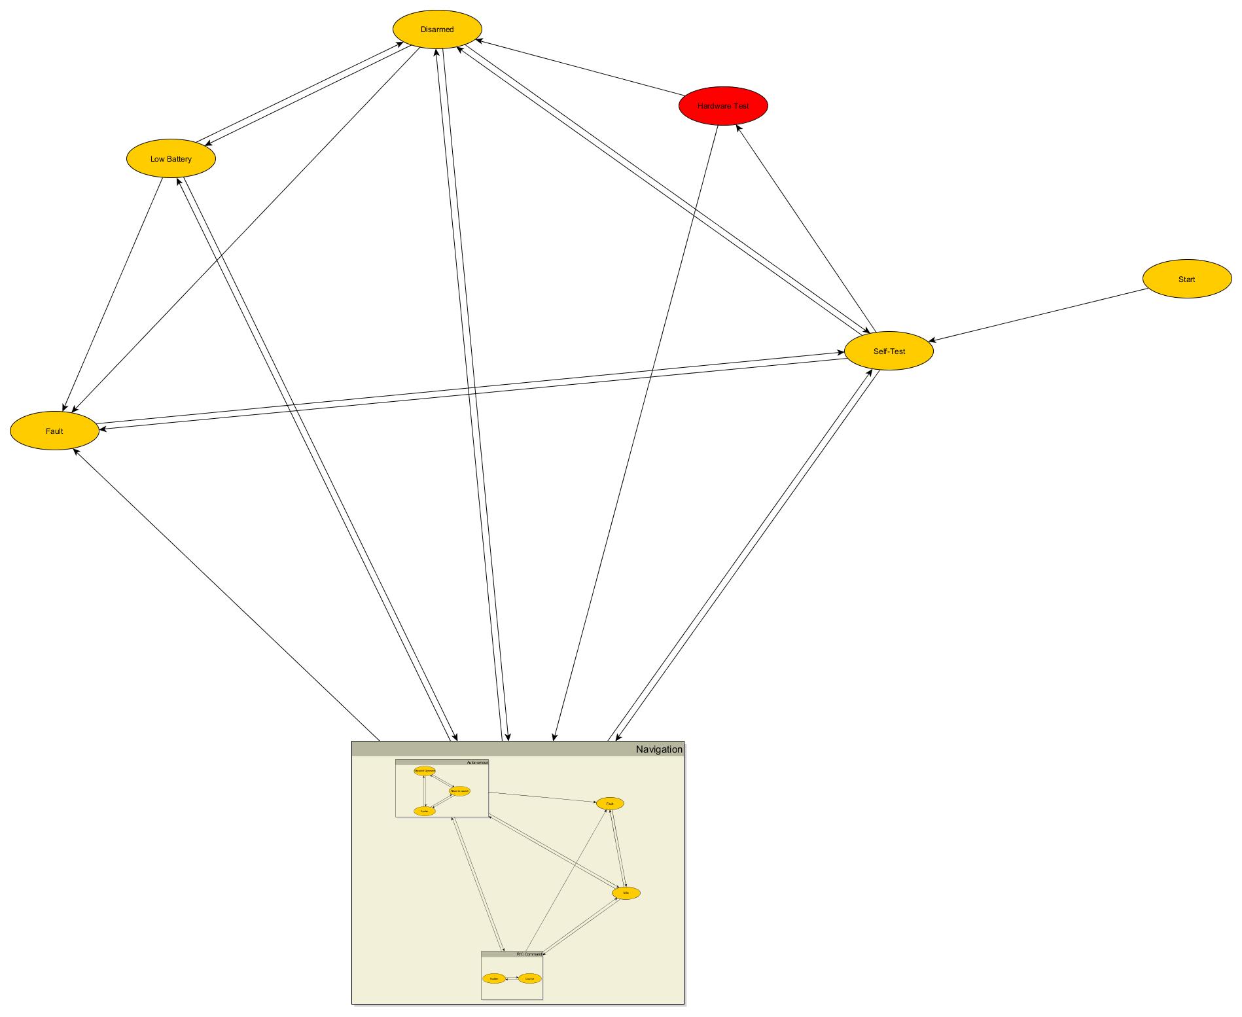
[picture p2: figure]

b) The modes shall be divided into levels for simplicity. Top level modes shall be as depicted in Figure 1.

Figure 1 Top Level Mode Diagram

c) All boat modes shall be subclasses of BoatModeBase.
d) BoatModeBase shall have a factory() method which takes a reference to a BoatState object and a BoatModeEnum variable. It shall return a pointer to a newly created object of the correct mode type.

### 2.3.1 Startup

a) The boat shall enter the Startup mode immediately on starting.
b) This mode shall place all outputs in a safe state.
c) This mode shall load a copy of the last BoatState object from the database. This allows the boat to resume its previous mode in case of an unexpected reboot.
d) The boat will transition to Self-Test on the first frame.

### 2.3.2 Self-Test

a) The Self-Test state shall determine whether all inputs and outputs of the system are functional.
b) The Self-Test state shall run for the period defined by SELFTEST_DELAY (located in hal/config.h). During that run, it shall monitor all inputs for fault states. The boat must be still during this period.
c) On the first frame of execution, this mode will make an object local copy of the old BoatState object and clear the fault string.
d) Self-test shall check the following parameters each frame during the test period:
  a. The main battery voltage is above the voltage defined in SYSTEM_START_BATTERY_MIN.
  b. The HealthMonitor object’s state is invalid.
  c. The RCInput object’s state is invalid.
  d. The ADCInput object’s state is invalid.
  e. The GPSInput object’s state is invalid.
  f. The GPS is not receiving valid fixes.
  g. The disarm input GPIO is not valid.
  h. The enable input GPIO is not valid.
  i. Any relay output is faulted.
e) The servo power shall be turned on in this mode.
f) Mode transitions shall not occur until after SELFTEST_DELAY has elapsed.
g) If the only fault present is low battery, the boat mode will transition to the Low Battery mode.
h) If any other faults are present, the boat mode will transition to the Fault mode.
i) If the boat mode in the stored BoatState object is Navigation and the enable GPIO input is high, then the boat shall transition into the Navigation mode with the same sub-mode as the old BoatState object.
j) Otherwise, the boat mode shall transition to the Disarmed mode.

### 2.3.3 Disarmed

a) The servo power shall be disabled.
b) The throttle shall be set to zero.
c) If the boat receives a Self-Test command from the shore, the boat shall transition to the Self-Test mode.
d) If the boat received a Navigation command from the shore, the boat shall pulse the Enable relay high.
e) If the enable GPIO input is high, this mode shall turn on the horn relay output for HORN_TIME.
f) Once HORN_TIME has elapsed, if the enable GPIO input is still high, the boat shall transition to the Navigation mode.

### 2.3.4 Low Battery

a) If the battery voltage has recovered above SYSTEM_START_BATTERY_MIN, the boat shall recover to the last good mode.
b) The servo power shall be disabled.
c) The throttle shall be set to zero.
d) If any other faults are detected while in this mode, the boat shall transition to fault mode.
e) The boat shall not accept mode commands while in this state.

### 2.3.5 Fault

a) This mode shall test each of the fault conditions listed in Self-Test and remove any fault conditions that have healed since entering fault mode.
b) The servo power shall be disabled.
c) The throttle shall be set to zero.
d) If all fault conditions have healed, the boat shall transition to the last good mode.

### 2.3.6 Navigation

a) The Navigation mode shall implement the next level down of the state machine. See the State Machine section for details.
b) The Servo power shall be turned on in this mode.
c) In the case of any state transition, the current navigation mode shall be preserved in the BoatState object.
d) If the boat receives a command to go into Self-Test or Disarmed, it shall transition into that state. All other state transition commands must be ignored.
e) After checking incoming commands, the Navigation mode shall call the current sub-mode’s execute() method.
f) If, after the sub-mode’s execute() method returns, the battery voltage is less than SYSTEM_LOW_BATTERY_CUTOFF, this method shall set a “Low Battery” fault and transition to the LowBattery mode.
g) If the BoatState has any other fault or the new navigation sub-mode is Fault, the boat shall transition to Fault mode.
h) If the disarm GPIO is high, the boat shall transition to the Disarmed mode.

#### 2.3.6.1 Idle

a) The Idle sub-mode shall center the rudder and set the throttle to zero.
b) The Idle sub-mode shall accept any command to change the current navigation mode.
c) The Idle sub-mode will check the RC/Auto switch on the remote control. If it is in the RC position, the boat shall transition to the RC sub-mode.
d) The Idle sub-mode shall check for faults in the rudder, throttle, servo power, ADC, orientation, and gps sub-systems.

#### 2.3.6.2 Fault

a) The Fault sub-mode shall center the rudder and set the throttle to zero.
b) The Fault sub-mode shall check if the fault states checked for in the other navigation sub-modes have cleared. If they have, it shall transition to the Idle sub-mode.

#### 2.3.6.3 RC Command

a) The RC mode shall implement the sub-modes described below. See the State Machine section for details.
b) The Servo power shall be turned on in this sub-mode.
c) This sub-mode shall monitor the servo enable, ADC, Orientation, and GPS for faults.
d) If the RC/Auto switch is set to Auto, the boat shall transition to the Autonomous sub-mode.
e) If the boat remains the Failsafe sub-mode for more than RETURN_TIMEOUT, the boat shall transition to the Autonomous->Return sub-mode of the Navigation mode.

##### 2.3.6.3.1 Idle

a) The idle sub-mode shall set the rudder and throttle to zero.
b) This sub-mode shall monitor the output of getMode() method of the RCInput object and transition to Rudder, Course, or Failsafe in response to controller switch positions.

##### 2.3.6.3.2 Course

a) The course sub-mode shall steer a compass course set by the manual remote control, as described in the R/C receiver section.
b) This sub-mode shall execute the helm Compute() mode on each iteration.
c) This sub-mode shall modify the PID constants in response to changes in the stored constants in the BoatMode object. Note that these modifications will typically be in response to a call to SetPID from the shore.
d) This sub-mode shall monitor the output of getMode() method of the RCInput object and transition to Rudder, Failsafe, or Idle in response to controller switch positions.
e) This sub-mode shall set the throttle to the value returned by getThrottle().

##### 2.3.6.3.3 Rudder

a) The rudder sub-mode shall set the rudder to the value returned by getRudder().
b) This sub-mode shall monitor the output of getMode() method of the RCInput object and transition to Course, Failsafe, or Idle in response to controller switch positions.
c) This sub-mode shall set the throttle to the value returned by getThrottle().

##### 2.3.6.3.4 Fail Safe

a) The failsafe sub-mode shall set the rudder and throttle to zero.
b) This sub-mode shall monitor the output of getMode() method of the RCInput object and transition to Rudder, Course, or Idle in response to controller switch positions.

#### 2.3.6.4 Autonomous

a) The Autonomous mode shall implement the sub-modes described below. See the State Machine section for details. The Servo power shall be turned on in this sub-mode.
b) If the RC/Auto switch is set to RC, the boat shall transition to the RC sub-mode.
c) The Autonomous sub-mode shall monitor the servo enable, ADC, Orientation, and GPS for faults.
d) The Autonomous sub-mode shall monitor for low battery conditions
e) The Autonomous sub-mode shall monitor for the command to disarm the boat.

##### 2.3.6.4.1 Idle

a) The Idle sub-mode shall set the rudder and throttle e to zero.
b) The Idle sub-mode shall accept and implement commands to change the Autonomous sub-mode to any other possible value (Waypoints, Return, or Anchor).

##### 2.3.6.4.2 Waypoint

a) The Waypoint sub-mode shall plot a course to the waypoint stored in the BoatState object’s waypoints list and indicated by the current waypoint number in the same object.
b) The plotted course shall be a great circle.
c) If the Obstacle Avoidance functionality has been implemented, the Waypoint mode shall use it to modify the plotted course to the next waypoint.
d) The Waypoints sub-mode shall use a PID loop with the constants stored in the BoatState object to set the rudder.
e) If the Obstacle Avoidance has been implanted, it shall set the throttle command. Otherwise, the throttle shall be set to AUTO_DEFAULT_THROTTLE in this mode.
f) When the boat comes within AUTO_WAYPOINT_TOL meters of the waypoint, it shall increment the waypoint selector to the next waypoint in the list.
g) If there is no next waypoint, this sub-mode shall reset the waypoint selector and/or transition modes as described in WaypointActionEnum.

##### 2.3.6.4.3 Return to Launch

a) The Return sub-mode shall obey the requirements of the Waypoint sub mode with the following exceptions:
  a. The target waypoint shall be the origin point stored in the BoatMode object.
  b. Upon reach the target, the boat shall transition to Anchor sub-mode.

##### 2.3.6.4.4 Anchor

a) In the Anchor sub-mode, the boat shall attempt to hold a given position.
b) If the target point is ahead of the boat, this sub-mode shall set forward throttle proportional[^13] to the position error distance. It shall also steer a direct course to the target point.
c) If the target point is ahead of the boat, this sub-mode shall set reverse throttle proportional to the position error distance. It shall also steer a reverse course[^14] to the target point.

# 3 External Utilities

## 3.1 User Interface

## 3.2 Remote Control Setup

## 3.3 Sailing Simulator

### 3.3.1 Phase 1

### 3.3.2 Phase 2

[^1] Sourced from http://www.cypress.com/file/130456/download
[^2] Note that the SSL code has not been implemented yet, because I have not figured out how to set it up correctly for the Paho client.
[^3] This has not yet been implemented due to concerns about Adafruit.io’s maximum element length.
[^4] Note that we use modes instead of states here in order to avoid excessive overloading of the term state.
[^5] Ch 4.4 of Arkin’s Behavior Based Robotics describes this as a schema-based behavior architecture. The two schemas at play here are move towards goal and avoid obstacles.
[^6] It’s not clear what value this ought to have – that should be determined by simulation and experiment.
[^7] The intent here is that if we are facing a wall, all the summed vectors shall point in the same direction and get us around the wall, rather than create a zero trap in the vector field.
[^8] The proportionality constant requires tuning.
[^9] The intent here is that if we have an obstacle to the left and the right, the resulting vectors will tend to push the boat towards the center course.
[^10] This is most likely going to be a buffer zone around land, known platforms, and the like.
[^11] The assumption here is that A*’s ‘best first’ nature will result in an optimal path. If multiple paths reach the goal, the clear heuristic to use is the one that contains less segments.
[^12] In the case of a steered course, the input is equal to the error and the setpoint is zero. The reason for this is because the simple calculation does not take into account the fact that compass course wraps around.
[^13] Eventually we’ll use a PID loop for this, but not right now.
[^14] I.e. 180 degrees out from the target course, since we’re trying to point the stern rather than the bow at the target in this case.

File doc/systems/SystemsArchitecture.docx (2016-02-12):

# Systems Architecture

# Hardware Architecture

The Hackerboat control system consists of three major components -- a shore station, a Beaglebone, and an Arduino Mega. The Beaglebone and the Arduino are located in a control box on the boat. They communicate with the shore station via a two-legged network. The Beaglebone is attached to a common carrier board with the Arduino. It communicates with the Arduino with two serial channels. It is connected to the network, housed in the radio box, via a WiFi link. The control box also contains an IMU (read by the Arduino) and a GPS (read by the Beaglebone).

The radio box contains two radios, the WiFi router and the 900 MHz router. Both are running OpenWRT. The 900 MHz router connects to the shore station, which is another, similar 900 MHz router.

See https://github.com/JeremyRuhland/hackerboat/blob/restful_refactor/doc/systems/Hackerboat-Systems-Diagram.graphml for a complete systems diagram.

# Software Architecture

## Responsibilities

The Beaglebone shall be the dominant partner between the two computers. The Arduino shall obey commands coming from it implicitly. It shall do all the high level course planning etc when the boat is autonomous mode. When the boat is in manual mode, it shall surrender high-level control to the shore station and shall take over if and only if the shore station stops transmitting commands. The Beaglebone shall receive position data from the GPS and shall poll ship status data from the Arduino.

The Arduino shall do all of the low level processing. It shall take compass data from the IMU and shall receive a target heading from either the Beaglebone or the shore station. It also shall record and report data from the various ship status sensors (voltages, currents, and so on) and the two buttons (stop and go). The Arduino shall control the throttle, the steering servo, the status lights, and the horn.

The shore station shall provide a method for the operator to arm the boat, provide steering and throttle commands, and to plot a course for the boat to follow in autonomous mode. It also shall provide the interface for the user to acquire data from the boat.

## Communications Channels

All primary communications between the three elements of the control system (shore, Beaglebone, and Arduino) shall be via REST requests from higher levels to lower ones. I.e. the shore station may send requests to the Beaglebone and the Arduino. The Beaglebone may send requests to the Arduino. Requests may not be sent in the other direction; only responses.

The communication links shall be as follows:

- TCP/IP connection between the shore station and the Beaglebone, as described in the Hardware Architecture section (above).
- The Control Serial link between the Beaglebone and the Arduino. This link shall be Serial1 on the Arduino side and UART2 on the Beaglebone side.
- The Log Serial link between the Arduino and the Beaglebone. This link shall be Serial on the Arduino side and UART1 on the Beaglebone side.

Requests from the shore station to the Beaglebone shall be sent over the TCP/IP link with http.[^1] The Beaglebone shall run a webserver to receive and dispatch these requests either to its own operating software or to the Arduino. Requests bound for the Arduino shall be dispatched to it via the Control Serial link, and responses are expected on the same serial link. Once a response is received by the Beaglebone from the Arduino, it shall pass that response along to the shore station.

The Beaglebone may send its own REST requests over the Control Serial link, and shall handle them as otherwise described in this document.

The Beaglebone shall also record all data transmitted by the Arduino on the Log Serial link to non-volatile storage for later retrieval and analysis. This may be done by the simple expedient of opening the serial port and piping all output to a disk file.

## Arduino Software

The Arduino software shall take the inputs described in this section, process them according to the rules laid out here, and produce the outputs described in the appropriate section. It shall be written in the standard Arduino language, and shall use only those libraries included as part of the Arduino core (i.e. by the statement #include <Arduino.h>) or listed below.

### Hardware

The Arduino hardware shall be an Arduino Mega 2560 or equivalent.

### Inputs

The Arduino shall read the follow inputs:

- Control Serial, on the Serial1 device
- IMU, on the I2C bus
- Start button, on pin 37
- Stop button, on pin 36
- Power input voltage, on pin A0
- Motor current, on pin A13
- Motor voltage, on pin A15

### Outputs

The Arduino shall write to the following outputs:

- Log Serial, on the Serial device
- Control Serial, on the Serial1 device
- Arduino status lights, on pin 39
- Beaglebone status lights, on pin 38
- Throttle relay drivers, as follows:
  - Direction relay, on pin 52
  - White speed relay, on pin 51
  - Yellow speed relay, on pin 48
  - Red speed relay, on pin 47
  - Red/White crossover relay, on pin 44
  - Red/Yellow crossover relay, on pin 43
- Horn relay driver, on pin 40
- Steering servo, on pin 3
- Steering servo power enable, on pin 2

### Execution Order

The execution of the code shall be divided into frames. Frames may be executed on a clock or may be free-running, as long as all timing constraints are observed.

Each frame shall consist of the following steps:

- Read all local inputs
- Check for incoming requests on Control Serial
- Process any incoming requests
- Perform operations required by the current state
- Select the state for the next frame
- Write to all outputs, including the Control and Log Serial channels.
- On each frame, the Arduino shall output its current state as a JSON string with no end of line terminations on its Control Serial channel.

### Non Volatile Memory

On the output phase of each frame in states other than Self-Test, Fault, and Power-Up, the Arduino code shall record the current state and the last state in three suitable locations in NVM.
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

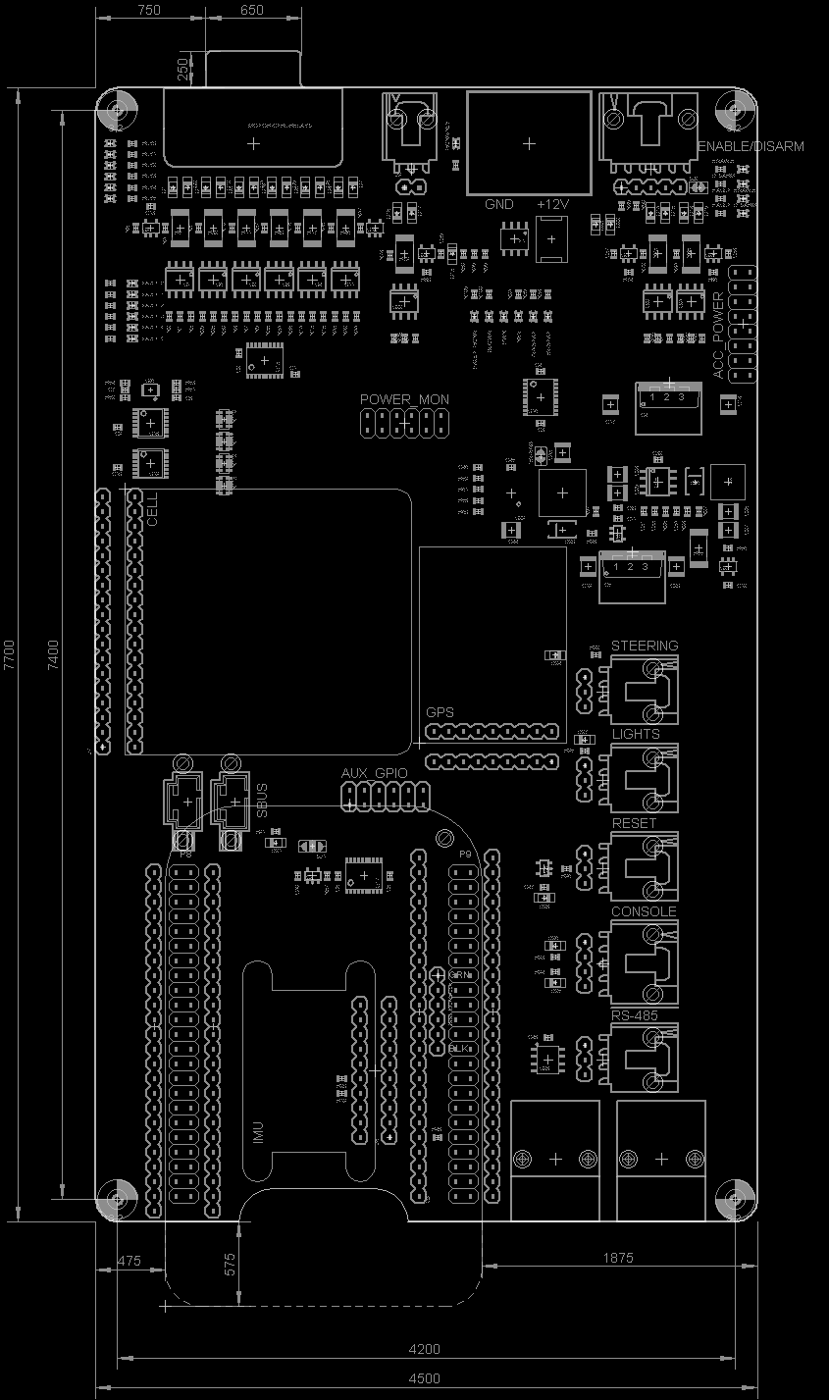
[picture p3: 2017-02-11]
hardware/electronics/ControlBoard/ControlBoard-mechanical.png

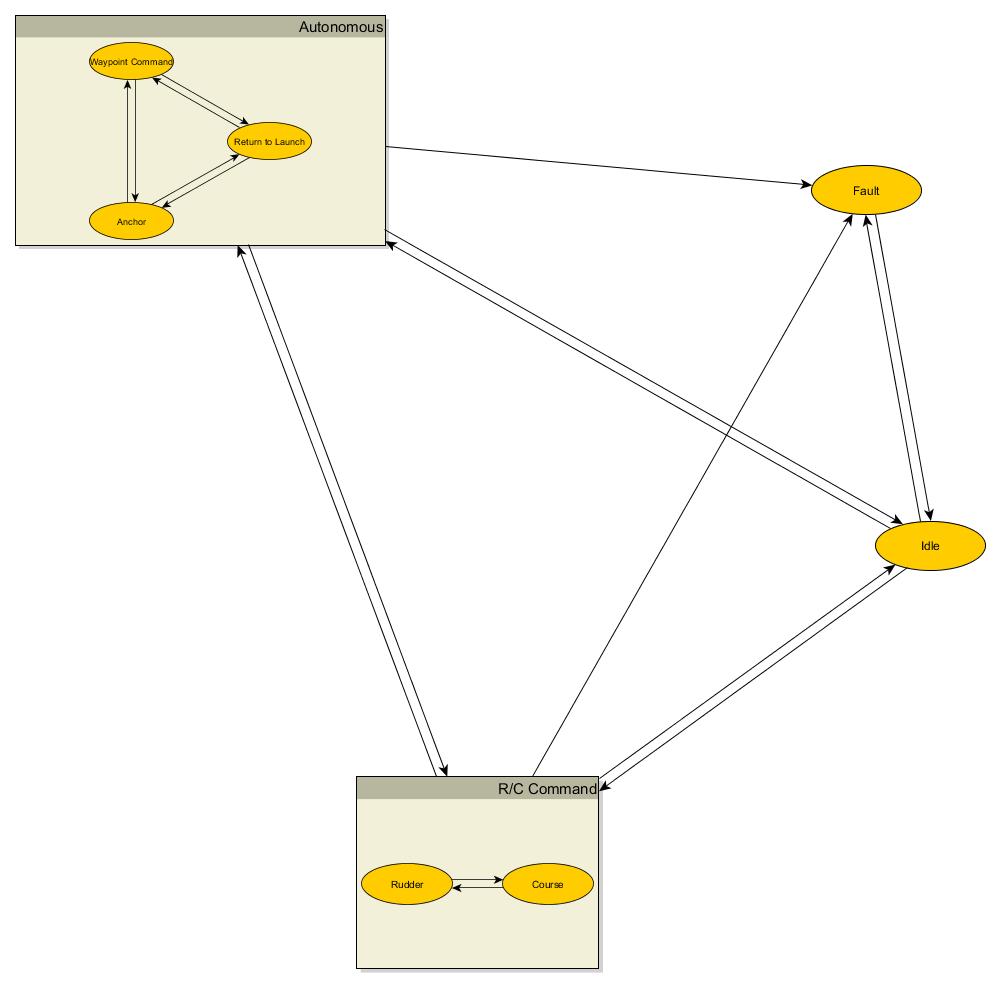
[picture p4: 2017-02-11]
doc/systems/Hackerboat-Modes-navigation.jpg

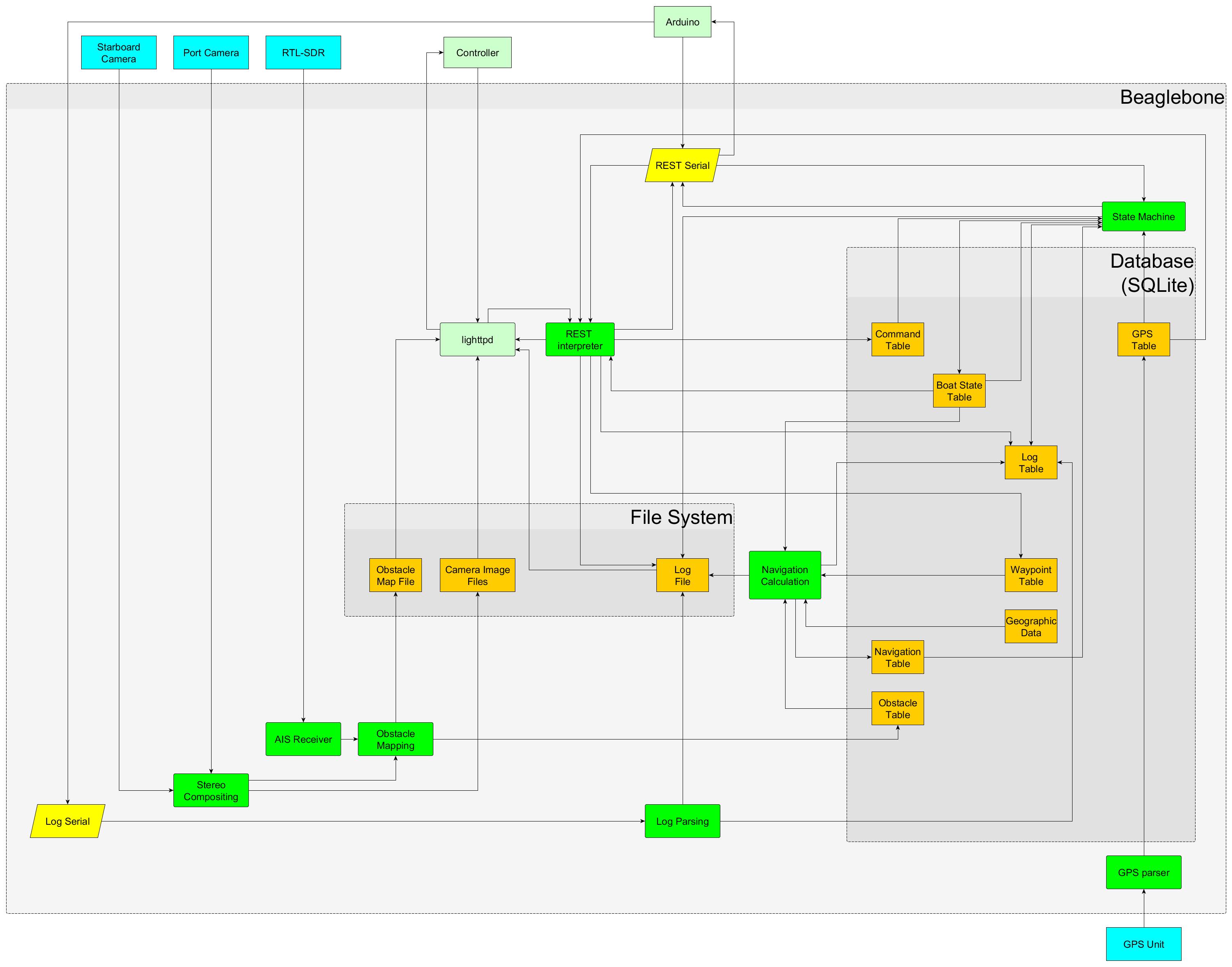
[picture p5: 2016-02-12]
embedded_software/dataflow-diagram.jpg

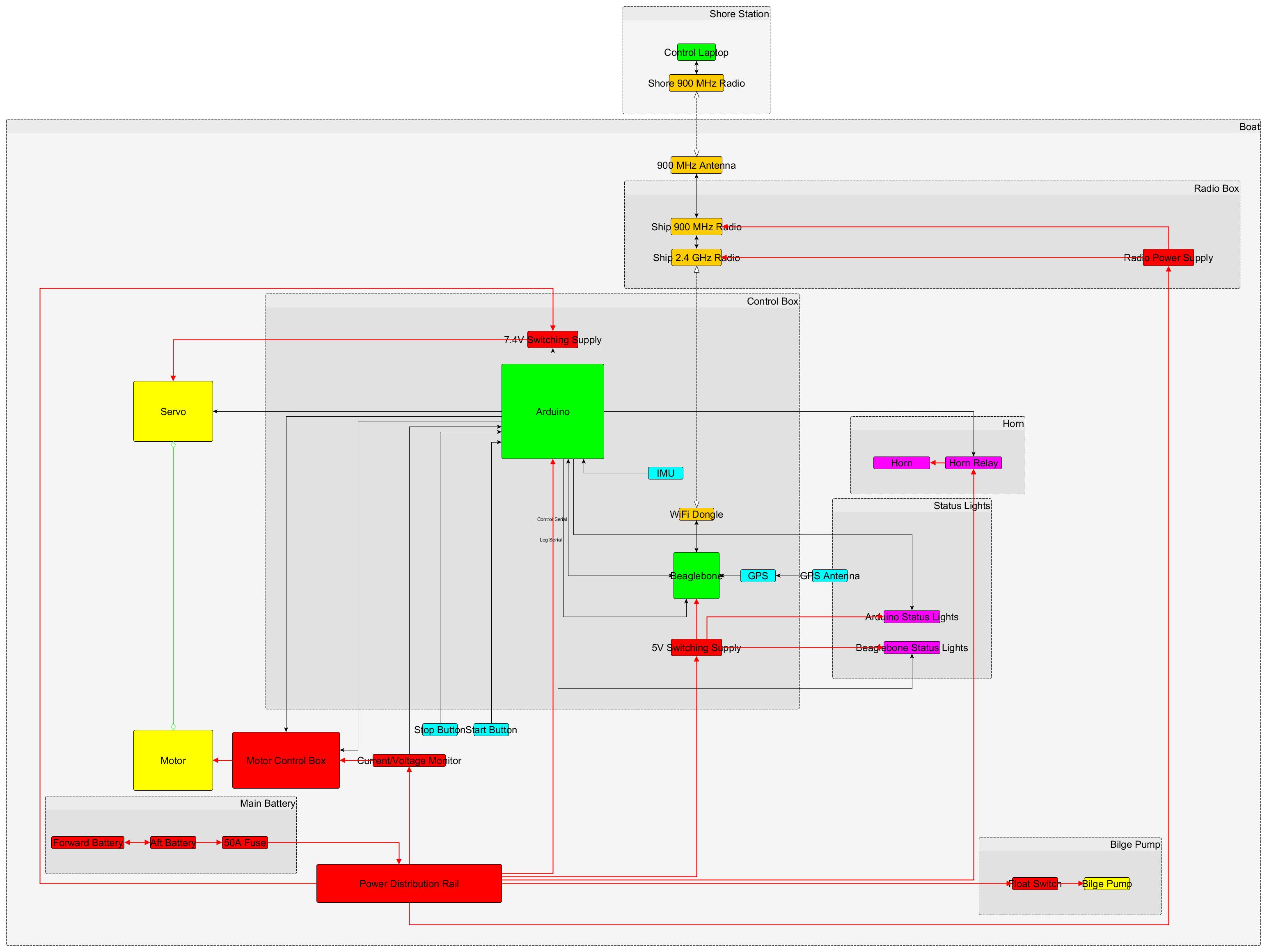
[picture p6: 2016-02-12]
embedded_software/Hackerboat-Systems-Diagram.jpg

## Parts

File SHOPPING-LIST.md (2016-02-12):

Mark items with a 'Yes' in the purchased column when ordered and cross them out when they are in hand. 

| Quantity | Item | Vendor | Link | Price | Purchased? | Est Delivery? |
|---|---|---|---|---|---|---|
| 1 | 2:1 steering ratio servo gear (32 tooth) | ServoCity | http://www.servocity.com/html/32p_hitec_metal_gear.html#.VCZduvldXZU | $14.99 | No |
| 1 | 2:1 steering ratio hub gear (64 tooth) | ServoCity | http://www.servocity.com/html/32_pitch_aluminum_hub_gears__1.html#.VCZdvPldXZU | $12.99 | No |

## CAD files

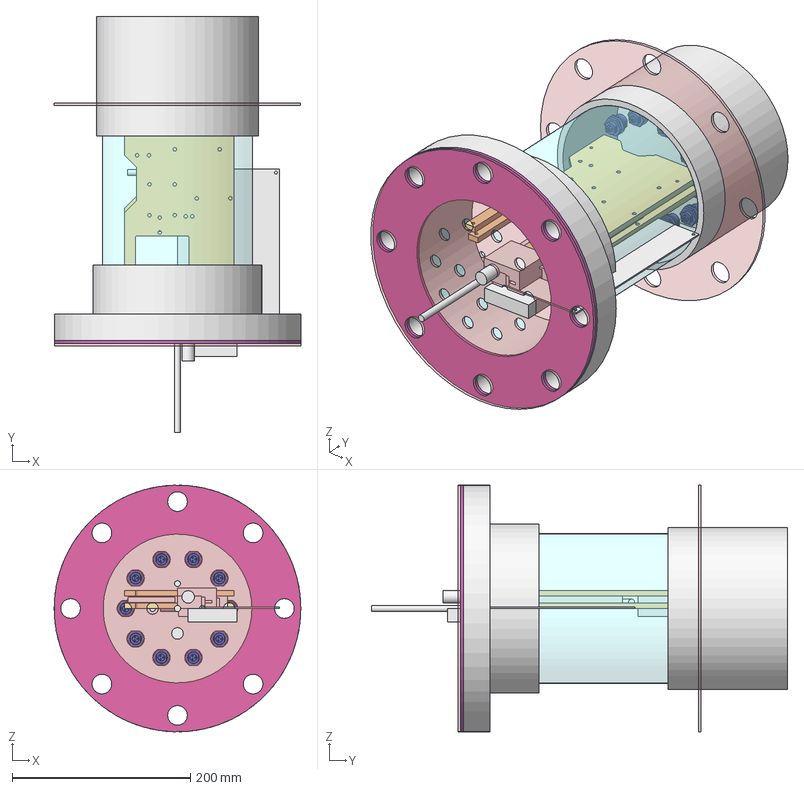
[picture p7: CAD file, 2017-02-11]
hardware/mounting/ElectronicsBoxes/drybox_mockup.fcstd
277.0 x 467.0 x 276.9 mm
SP13
Clone of SP13
Clone of SP014
Clone of SP015
Clone of SP016
Clone of SP017
Clone of SP018
Clone of SP019
Clone of SP020
Clone of SP021
Clone of SP022
Receiver
Antenna
Transceiver
Antenna001

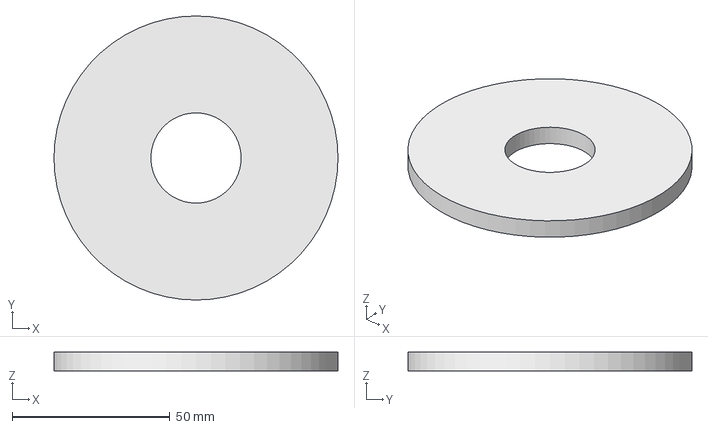
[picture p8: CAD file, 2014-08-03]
hardware/mounting/SteeringServo/control-arm-spacer-1.FCStd
90.0 x 90.0 x 6.00 mm

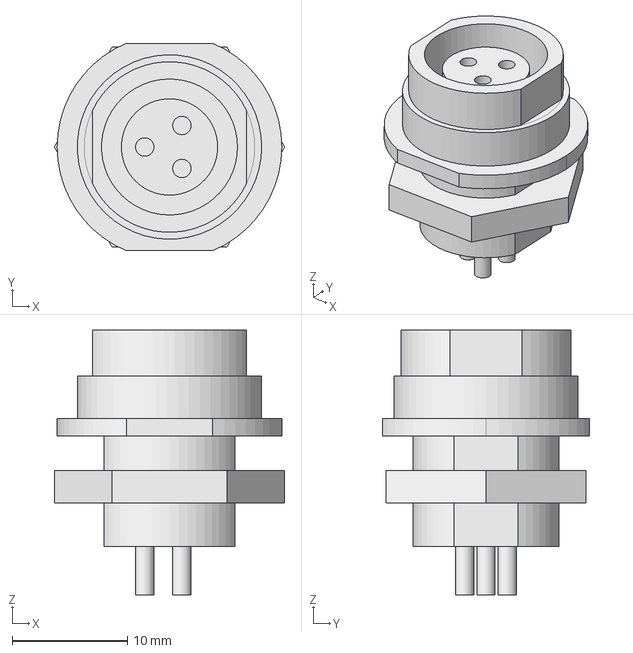
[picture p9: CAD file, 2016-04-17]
hardware/mounting/StereoEyes/COTS_models/sp1312_panel_mount_connector.step
20.0 x 18.0 x 23.0 mm

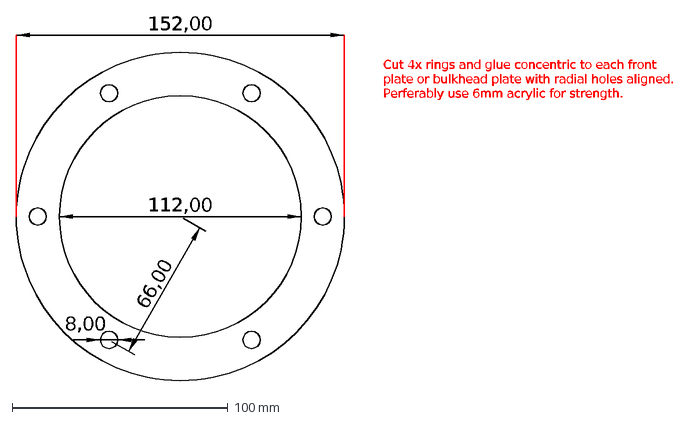
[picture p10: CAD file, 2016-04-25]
hardware/mounting/StereoEyes/retaining_ring.dxf
112,00
152,00
66,00
Cut 4x rings and glue concentric to each front plate or bulkhead plate with radial holes aligned. Perferably use 6mm acrylic for strength.
8,00

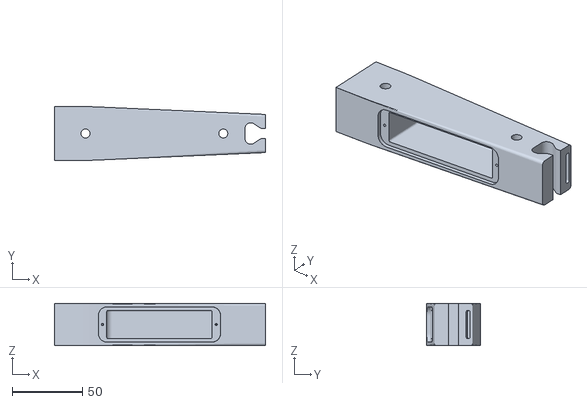
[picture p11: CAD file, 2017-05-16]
hardware/wings/subscale-wing/stls/BoomForward.stl
150.0 x 38.2 x 30.0

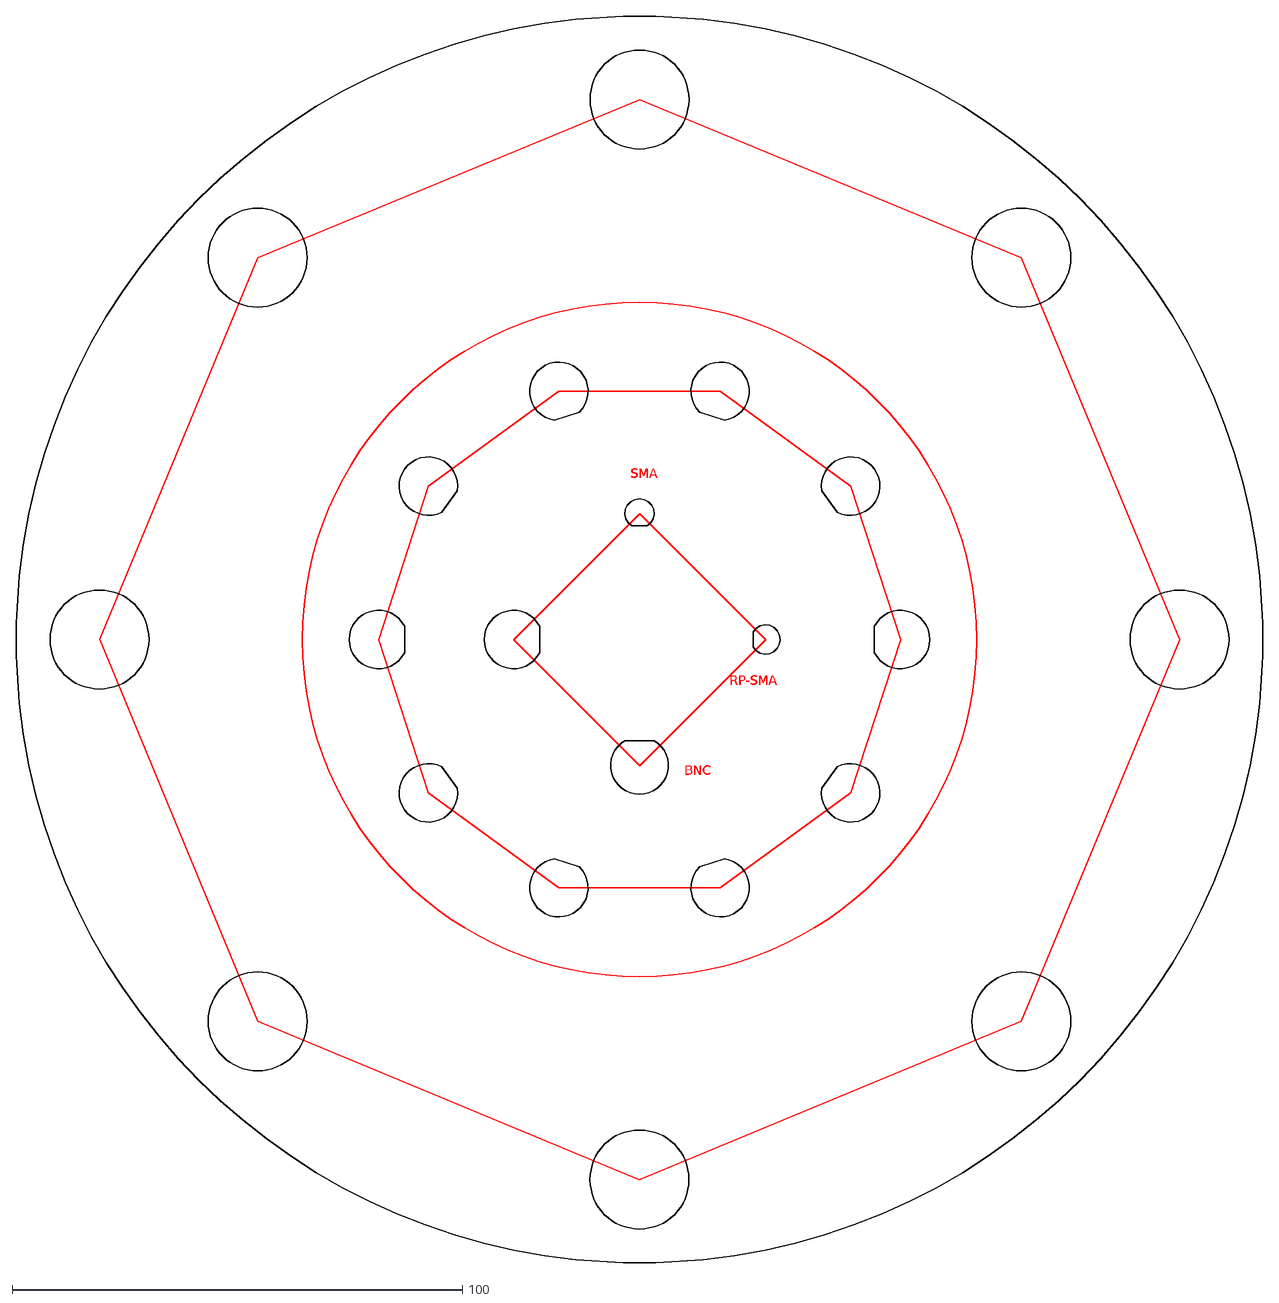
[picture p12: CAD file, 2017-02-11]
hardware/mounting/ElectronicsBoxes/bulkhead_passthroughs.dxf
SMA
RP-SMA
BNC

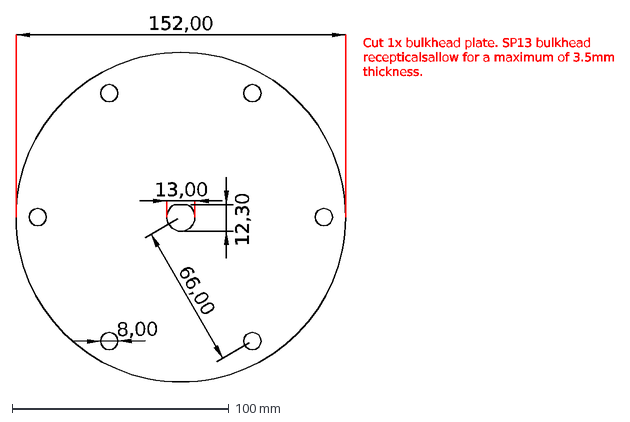
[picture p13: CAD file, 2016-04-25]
hardware/mounting/StereoEyes/bulkhead_plate.dxf
8,00
66,00
152,00
13,00
12,30
Cut 1x bulkhead plate. SP13 bulkhead recepticals allow for a maximum of 3.5mm thickness.

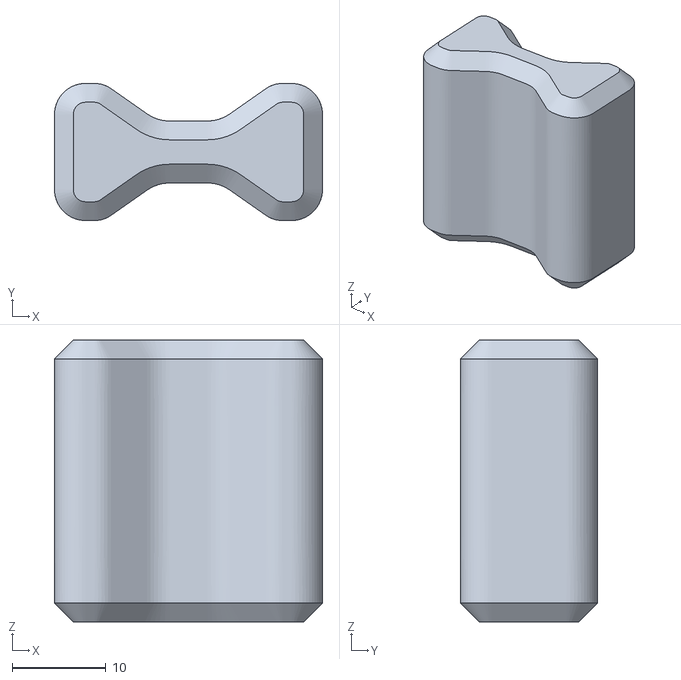
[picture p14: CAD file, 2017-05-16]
hardware/wings/subscale-wing/stls/Dogbone.stl
28.5 x 14.6 x 30.0

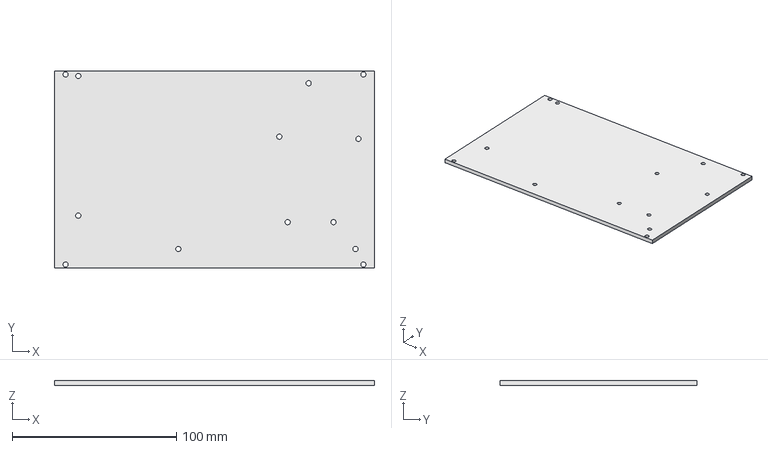
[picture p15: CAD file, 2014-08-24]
hardware/mounting/ElectronicsBoxes/controls-mounting-plate.FCStd
195.0 x 120.0 x 3.00 mm

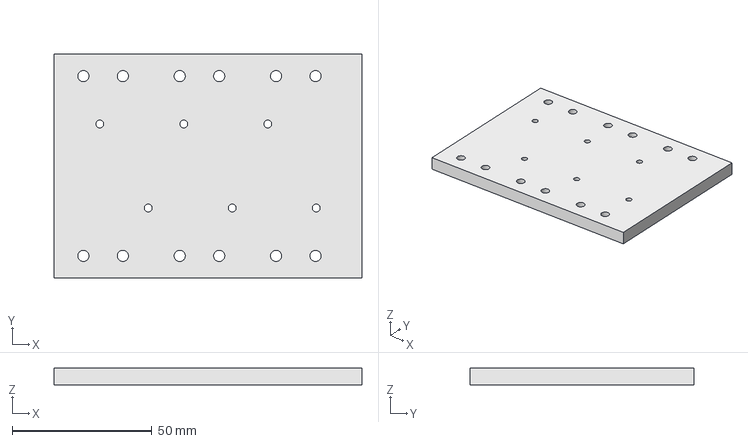
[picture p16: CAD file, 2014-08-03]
hardware/mounting/SteeringServo/HackerBoat-Servo-Mount.FCStd
110.0 x 80.0 x 6.00 mm

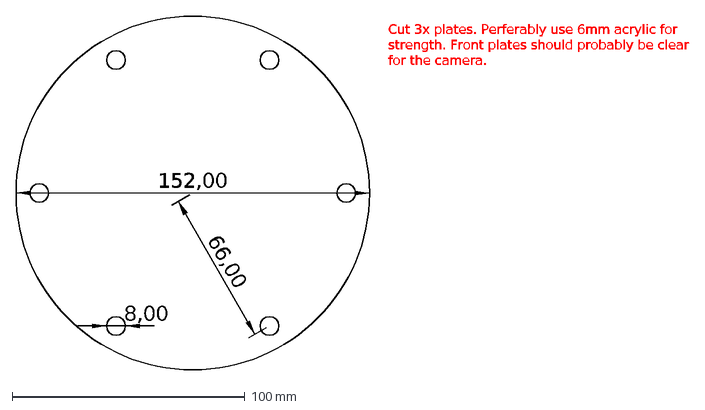
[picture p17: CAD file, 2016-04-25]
hardware/mounting/StereoEyes/front_plate.dxf
152,00
8,00
66,00
Cut 3x plates. Perferably use 6mm acrylic for strength. Front plates should probably be clear for the camera.

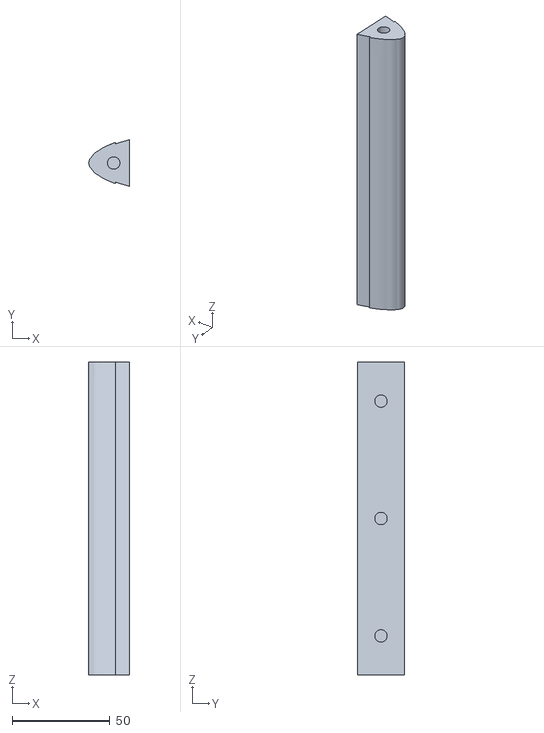
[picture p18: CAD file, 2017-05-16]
hardware/wings/subscale-wing/stls/LeadingEdgeSection.stl
20.8 x 23.8 x 160.0

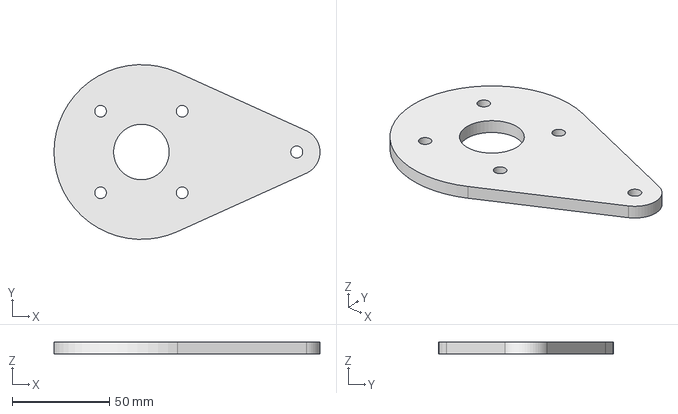
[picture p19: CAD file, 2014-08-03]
hardware/mounting/SteeringServo/control-arm.FCStd
137.0 x 89.9 x 6.00 mm

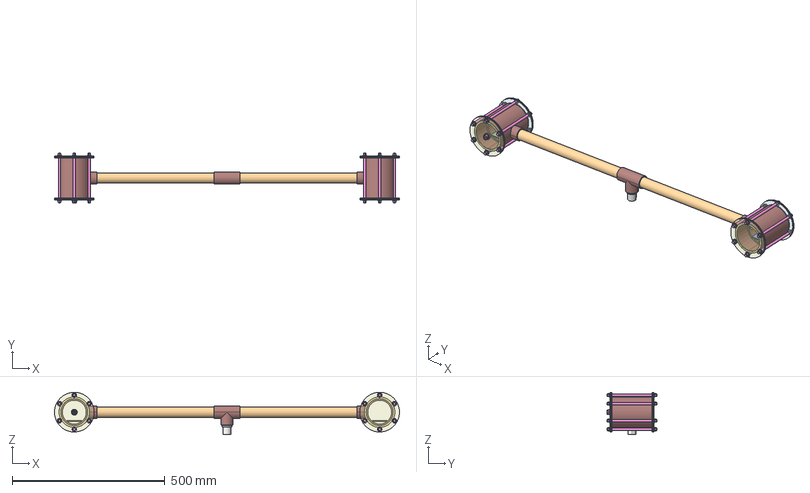
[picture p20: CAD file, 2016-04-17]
hardware/mounting/StereoEyes/StereoEyes.FCStd
1129.9 x 164.0 x 138.8 mm
TL 3in/1in T joint right
TL 1in PCV right
TL 1in PCV left
TL webcam stand right
TL webcam stand left
TL 1in PVB T joint center
TL acrylic window holes right rear
TL acyrlic window retainer holes right rear
TL rubber sealing gasket right rear
TL 1in pipe connector center
TL 3in/1in T joint left
TL acrylic window holes right front
TL acyrlic window retainer holes right front
TL rubber sealing gasket right front
TL acrylic window holes left rear
TL acyrlic window retainer holes left rear
TL rubber sealing gasket left rear
TL acyrlic window retainer holes left front
TL rubber sealing gasket left front
TL 1in PVC center coupler
TL acrylic window holes panel mount left front
TL bulkhead electrical connector left
TL waterproof plug center
TL thread rod 7 right 1
TL thread rod 7 right 2
TL thread rod 7 right 3
TL thread rod 7 right 4
TL thread rod 7 right 5
TL thread rod 7 right 6
TL thread rod 7 left 1
TL thread rod 7 left 2
TL thread rod 7 left 3
TL thread rod 7 left 4
TL thread rod 7 left 5
TL thread rod 7 left 6

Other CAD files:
hardware/mounting/SteeringServo/control-arm-spacer-2.FCStd
hardware/mounting/ElectronicsBoxes/relay-mounting-plate.FCStd
hardware/wings/subscale-wing/stls/LowerTailPlane.stl
hardware/wings/subscale-wing/stls/UpperTailPlane.stl
hardware/mounting/StereoEyes/COTS_models/4880K430.STEP
hardware/mounting/StereoEyes/COTS_models/4880K583.STEP
hardware/mounting/StereoEyes/COTS_models/4880K785.STEP
hardware/wings/subscale-wing/stls/BoomAft.stl
hardware/wings/subscale-wing/stls/CounterweightMount.stl
hardware/wings/subscale-wing/stls/ElectronicsHatch.stl

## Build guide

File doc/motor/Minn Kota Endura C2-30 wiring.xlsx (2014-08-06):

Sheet: Control Switch
 | Connections
Switch Position | White | Red | Yellow | Black
F5 | Batt+ | Batt+ | Batt+ | Batt-
F4 | Red | White | Batt+ | Batt-
F3 | Batt+ | N/C | Batt+ | Batt-
F2 | Batt+ | Yellow | Red | Batt-
F1 | Batt+ | N/C | N/C | Batt-
Off | N/C | N/C | N/C | N/C
R1 | Batt- | N/C | N/C | Batt+
R2 | Batt- | N/C | Batt- | Batt+
R3 | Batt- | Batt- | Batt- | Batt+

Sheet: Winding Resistance
 | Wht | Red | Ylw | Blk
White | * | 1R3 | 0R8 | 3R3
Red | 1R3 | * | 0R5 | 2R2
Yellow | 0R8 | 0R5 | * | 2R6
Black | 3R3 | 2R2 | 2R6 | *

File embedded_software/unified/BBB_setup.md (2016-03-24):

## Networking setup 

Add the following lines to /etc/network/interfaces:

```
auto wlan0
iface wlan0 inet dhcp
    wpa-ssid <boat ssid>
    wpa-psk  <boat psk>
```

Generate wpa-psk by running the following command:

```
$ wpa_passphrase <boat ssid> <boat passphrase>
```

## Software installations

Run the following installation commands:

```
$ sudo apt-get update
$ sudo apt-get upgrade
$ sudo apt-get install lighttpd libsqlite3-dev libfcgi-dev cmake automake
$ sudo apt-get install sqlite3 libgtest-dev
$ git clone --recursive https://github.com/JeremyRuhland/hackerboat.git
```

## rc.d changes

Run the following commands:

```
# update-rc.d -f apache2 remove
# update-rc.d -f lighttpd defaults
```

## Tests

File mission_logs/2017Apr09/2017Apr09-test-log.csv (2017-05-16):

main-20_46.log:2017Apr09-20:46:30:688 | INFO | ,CSV,RecordTime,CurrentWaypoint,WaypointStrength,/*LastContactTime,LastRCTime,*/Lat,Lon,Track,Speed,FixValid,StopButtonState,ArmButtonState,ServoEnableState,ThrottlePosition,RudderCommand,CurrentHeading,ThrottleInput,CourseInput,RCFailSafe,RCMode,RawMotorCurrent,RawBatteryVoltage
main-20_46.log:2017Apr09-20:47:04:068 | INFO | ,CSV,RecordTime,CurrentWaypoint,WaypointStrength,/*LastContactTime,LastRCTime,*/Lat,Lon,Track,Speed,FixValid,StopButtonState,ArmButtonState,ServoEnableState,ThrottlePosition,RudderCommand,CurrentHeading,ThrottleInput,CourseInput,RCFailSafe,RCMode,RawMotorCurrent,RawBatteryVoltage
main-20_46.log:2017Apr09-20:47:07:358 | INFO | ,CSV,2017-04-09 20:47:07.357,-1228750296,0.000000,47.592597,-122.382938,36.260000,0.237000,0,1,1, ,0,1500,225.504926,-6,-37.536585,
main-20_46.log:2017Apr09-20:47:07:860 | INFO | ,CSV,2017-04-09 20:47:07.858,-1228750296,0.000000,47.592593,-122.382950,28.530000,0.288000,0,1,1, ,0,1500,225.904358,-6,-37.536585,
main-20_46.log:2017Apr09-20:47:08:364 | INFO | ,CSV,2017-04-09 20:47:08.361,-1228750296,0.000000,47.592593,-122.382950,28.530000,0.288000,0,1,1, ,0,1500,225.152187,-6,-37.536585,
main-20_46.log:2017Apr09-20:47:08:902 | INFO | ,CSV,2017-04-09 20:47:08.863,-1228750296,0.000000,47.592630,-122.382943,23.780000,0.360000,0,1,1, ,0,1500,223.682325,-6,-37.536585,
main-20_46.log:2017Apr09-20:47:09:372 | INFO | ,CSV,2017-04-09 20:47:09.367,-1228750296,0.000000,47.592630,-122.382943,23.780000,0.360000,0,1,1, ,0,1500,228.147620,-6,-37.536585,
main-20_46.log:2017Apr09-20:47:09:876 | INFO | ,CSV,2017-04-09 20:47:09.873,-1228750296,0.000000,47.592665,-122.382930,24.460000,0.417000,0,1,1, ,0,1500,225.066209,-6,-37.536585,
main-20_46.log:2017Apr09-20:47:10:376 | INFO | ,CSV,2017-04-09 20:47:10.374,-1228750296,0.000000,47.592665,-122.382930,24.460000,0.417000,0,1,1, ,0,1500,224.502941,-6,-37.536585,
main-20_46.log:2017Apr09-20:47:10:880 | INFO | ,CSV,2017-04-09 20:47:10.877,-1228750296,0.000000,47.592682,-122.382923,24.460000,1.920000,0,1,1, ,0,1500,224.243440,-6,-37.536585,
main-20_46.log:2017Apr09-20:47:11:380 | INFO | ,CSV,2017-04-09 20:47:11.378,-1228750296,0.000000,47.592682,-122.382923,32.540000,0.376000,0,1,1, ,0,1500,225.187414,-6,-37.536585,
main-20_46.log:2017Apr09-20:47:11:884 | INFO | ,CSV,2017-04-09 20:47:11.880,-1228750296,0.000000,47.592688,-122.382923,38.110000,0.278000,0,1,1, ,0,1500,223.166366,-6,-37.536585,
main-20_46.log:2017Apr09-20:47:12:386 | INFO | ,CSV,2017-04-09 20:47:12.382,-1228750296,0.000000,47.592688,-122.382923,38.110000,0.278000,0,1,1, ,0,1500,226.065671,-6,-37.536585,
main-20_46.log:2017Apr09-20:47:12:886 | INFO | ,CSV,2017-04-09 20:47:12.884,-1228750296,0.000000,47.592702,-122.382913,40.250000,0.268000,0,1,1, ,0,1500,225.056225,-6,-37.536585,
main-20_46.log:2017Apr09-20:47:13:388 | INFO | ,CSV,2017-04-09 20:47:13.386,-1228750296,0.000000,47.592702,-122.382913,40.250000,0.268000,0,1,1, ,0,1500,225.289889,-6,-37.536585,
main-20_46.log:2017Apr09-20:47:13:888 | INFO | ,CSV,2017-04-09 20:47:13.887,-1228750296,0.000000,47.592715,-122.382907,25.240000,0.268000,0,1,1, ,0,1500,224.109807,-6,-37.536585,
main-20_46.log:2017Apr09-20:47:14:390 | INFO | ,CSV,2017-04-09 20:47:14.388,-1228750296,0.000000,47.592715,-122.382907,25.240000,0.268000,0,1,1, ,0,1500,225.047753,-6,-37.536585,
main-20_46.log:2017Apr09-20:47:14:896 | INFO | ,CSV,2017-04-09 20:47:14.894,-1228750296,0.000000,47.592717,-122.382905,23.740000,0.262000,0,1,1, ,0,1500,225.265255,-6,-37.536585,
main-20_46.log:2017Apr09-20:47:15:402 | INFO | ,CSV,2017-04-09 20:47:15.400,-1228750296,0.000000,47.592717,-122.382905,23.740000,0.262000,0,1,1, ,0,1500,227.084469,-6,-37.536585,
main-20_46.log:2017Apr09-20:47:15:909 | INFO | ,CSV,2017-04-09 20:47:15.907,-1228750296,0.000000,47.592723,-122.382898,34.360000,0.237000,0,1,1, ,0,1500,226.202018,-6,-37.536585,
main-20_46.log:2017Apr09-20:47:16:413 | INFO | ,CSV,2017-04-09 20:47:16.411,-1228750296,0.000000,47.592723,-122.382898,34.360000,0.237000,0,1,1, ,0,1500,224.839399,-6,-37.536585,
main-20_46.log:2017Apr09-20:47:16:918 | INFO | ,CSV,2017-04-09 20:47:16.914,-1228750296,0.000000,47.592728,-122.382897,38.510000,0.247000,0,1,1, ,0,1500,226.765302,-6,-37.536585,
main-20_46.log:2017Apr09-20:47:17:417 | INFO | ,CSV,2017-04-09 20:47:17.416,-1228750296,0.000000,47.592728,-122.382897,38.510000,0.247000,0,1,1, ,0,1500,225.504336,-6,-37.536585,
main-20_46.log:2017Apr09-20:47:17:919 | INFO | ,CSV,2017-04-09 20:47:17.917,-1228750296,0.000000,47.592727,-122.382900,50.680000,0.231000,0,1,1, ,0,1500,224.692912,-6,-37.536585,
main-20_46.log:2017Apr09-20:47:18:423 | INFO | ,CSV,2017-04-09 20:47:18.419,-1228750296,0.000000,47.592727,-122.382900,50.680000,0.231000,0,1,1, ,0,1500,223.654706,-6,-37.536585,
main-20_46.log:2017Apr09-20:47:18:922 | INFO | ,CSV,2017-04-09 20:47:18.921,-1228750296,0.000000,47.592727,-122.382900,52.580000,0.247000,0,1,1, ,0,1500,226.561429,-6,-37.536585,
main-20_46.log:2017Apr09-20:47:19:426 | INFO | ,CSV,2017-04-09 20:47:19.424,-1228750296,0.000000,47.592727,-122.382900,52.580000,0.247000,0,1,1, ,0,1500,225.589867,-6,-37.536585,
main-20_46.log:2017Apr09-20:47:19:927 | INFO | ,CSV,2017-04-09 20:47:19.926,-1228750296,0.000000,47.592733,-122.382897,49.560000,0.283000,0,1,1, ,0,1500,225.818518,-6,-37.536585,
main-20_46.log:2017Apr09-20:47:20:429 | INFO | ,CSV,2017-04-09 20:47:20.428,-1228750296,0.000000,47.592733,-122.382897,49.560000,0.283000,0,1,1, ,0,1500,224.907940,-6,-37.536585,
main-20_46.log:2017Apr09-20:47:20:932 | INFO | ,CSV,2017-04-09 20:47:20.931,-1228750296,0.000000,47.592737,-122.382893,52.690000,0.257000,0,1,1, ,0,1500,226.420266,-6,-37.536585,
main-20_46.log:2017Apr09-20:47:21:441 | INFO | ,CSV,2017-04-09 20:47:21.439,-1228750296,0.000000,47.592737,-122.382893,52.690000,0.257000,0,1,1, ,0,1500,226.565822,-6,-37.536585,
main-20_46.log:2017Apr09-20:47:21:945 | INFO | ,CSV,2017-04-09 20:47:21.943,-1228750296,0.000000,47.592738,-122.382892,51.400000,0.206000,0,1,1, ,0,1500,225.430748,-6,-37.536585,
main-20_46.log:2017Apr09-20:47:22:458 | INFO | ,CSV,2017-04-09 20:47:22.456,-1228750296,0.000000,47.592738,-122.382892,51.400000,0.206000,0,1,1, ,0,1500,224.853205,-6,-37.536585,
main-20_46.log:2017Apr09-20:47:22:960 | INFO | ,CSV,2017-04-09 20:47:22.958,-1228750296,0.000000,47.592742,-122.382890,45.600000,0.206000,0,1,1, ,0,1500,223.155905,-6,-37.536585,
main-20_46.log:2017Apr09-20:47:23:463 | INFO | ,CSV,2017-04-09 20:47:23.460,-1228750296,0.000000,47.592742,-122.382890,45.600000,0.206000,0,1,1, ,0,1500,226.089691,-6,-37.536585,
main-20_46.log:2017Apr09-20:47:23:964 | INFO | ,CSV,2017-04-09 20:47:23.962,-1228750296,0.000000,47.592745,-122.382888,38.450000,0.231000,0,1,1, ,0,1500,224.059616,-6,-37.536585,
main-20_46.log:2017Apr09-20:47:24:465 | INFO | ,CSV,2017-04-09 20:47:24.464,-1228750296,0.000000,47.592745,-122.382888,38.450000,0.231000,0,1,1, ,0,1500,226.736998,-6,-37.536585,
main-20_46.log:2017Apr09-20:47:24:966 | INFO | ,CSV,2017-04-09 20:47:24.965,-1228750296,0.000000,47.592747,-122.382887,35.600000,0.242000,0,1,1, ,0,1500,226.507256,-6,-37.536585,
main-20_46.log:2017Apr09-20:47:25:469 | INFO | ,CSV,2017-04-09 20:47:25.467,-1228750296,0.000000,47.592747,-122.382887,35.600000,0.242000,0,1,1, ,0,1500,224.822582,-6,-37.536585,
main-20_46.log:2017Apr09-20:47:25:970 | INFO | ,CSV,2017-04-09 20:47:25.968,-1228750296,0.000000,47.592752,-122.382882,30.160000,0.283000,0,1,1, ,0,1500,225.715510,-6,-37.536585,
main-20_46.log:2017Apr09-20:47:26:472 | INFO | ,CSV,2017-04-09 20:47:26.470,-1228750296,0.000000,47.592752,-122.382882,30.160000,0.283000,0,1,1, ,0,1500,226.502362,-6,-37.536585,
main-20_46.log:2017Apr09-20:47:26:975 | INFO | ,CSV,2017-04-09 20:47:26.972,-1228750296,0.000000,47.592758,-122.382878,28.160000,0.329000,0,1,1, ,0,1500,225.846540,-6,-37.536585,
main-20_46.log:2017Apr09-20:47:27:477 | INFO | ,CSV,2017-04-09 20:47:27.474,-1228750296,0.000000,47.592762,-122.382877,28.160000,0.391000,0,1,1, ,0,1500,224.501081,-6,-37.536585,
main-20_46.log:2017Apr09-20:47:27:986 | INFO | ,CSV,2017-04-09 20:47:27.985,-1228750296,0.000000,47.592762,-122.382877,27.300000,0.345000,0,1,1, ,0,1500,225.430042,-6,-37.536585,
main-20_46.log:2017Apr09-20:47:28:495 | INFO | ,CSV,2017-04-09 20:47:28.489,-1228750296,0.000000,47.592762,-122.382877,27.300000,0.345000,0,1,1, ,0,1500,225.772459,-6,-37.536585,
main-20_46.log:2017Apr09-20:47:28:992 | INFO | ,CSV,2017-04-09 20:47:28.990,-1228750296,0.000000,47.592763,-122.382872,34.050000,0.340000,0,1,1, ,0,1500,224.618874,-6,-37.536585,
main-20_46.log:2017Apr09-20:47:29:497 | INFO | ,CSV,2017-04-09 20:47:29.493,-1228750296,0.000000,47.592767,-122.382870,34.050000,0.391000,0,1,1, ,0,1500,224.274748,-6,-37.536585,
main-20_46.log:2017Apr09-20:47:29:999 | INFO | ,CSV,2017-04-09 20:47:29.994,-1228750296,0.000000,47.592767,-122.382870,30.750000,0.340000,0,1,1, ,0,1500,225.423969,-6,-37.536585,
main-20_46.log:2017Apr09-20:47:30:498 | INFO | ,CSV,2017-04-09 20:47:30.497,-1228750296,0.000000,47.592770,-122.382870,30.750000,0.371000,0,1,1, ,0,1500,224.165187,-6,-37.536585,
main-20_46.log:2017Apr09-20:47:31:004 | INFO | ,CSV,2017-04-09 20:47:31.001,-1228750296,0.000000,47.592770,-122.382870,25.500000,0.329000,0,1,1, ,0,1500,226.350027,-6,-37.536585,
main-20_46.log:2017Apr09-20:47:31:505 | INFO | ,CSV,2017-04-09 20:47:31.503,-1228750296,0.000000,47.592772,-122.382870,25.500000,0.185000,0,1,1, ,0,1500,225.397253,-6,-37.536585,
main-20_46.log:2017Apr09-20:47:32:008 | INFO | ,CSV,2017-04-09 20:47:32.006,-1228750296,0.000000,47.592772,-122.382870,24.610000,0.324000,0,1,1, ,0,1500,223.588571,-6,-37.536585,
main-20_46.log:2017Apr09-20:47:32:509 | INFO | ,CSV,2017-04-09 20:47:32.508,-1228750296,0.000000,47.592777,-122.382868,24.610000,0.570000,0,1,1, ,0,1500,225.347280,-6,-37.536585,
main-20_46.log:2017Apr09-20:47:33:012 | INFO | ,CSV,2017-04-09 20:47:33.009,-1228750296,0.000000,47.592777,-122.382868,24.770000,0.350000,0,1,1, ,0,1500,224.584644,-6,-37.536585,
main-20_46.log:2017Apr09-20:47:33:513 | INFO | ,CSV,2017-04-09 20:47:33.511,-1228750296,0.000000,47.592782,-122.382865,24.770000,0.610000,0,1,1, ,0,1500,225.649359,-6,-37.536585,
main-20_46.log:2017Apr09-20:47:34:030 | INFO | ,CSV,2017-04-09 20:47:34.028,-1228750296,0.000000,47.592782,-122.382865,25.810000,0.381000,0,1,1, ,0,1500,225.035362,-6,-37.536585,
main-20_46.log:2017Apr09-20:47:34:551 | INFO | ,CSV,2017-04-09 20:47:34.530,-1228750296,0.000000,47.592780,-122.382867,25.810000,0.224000,0,1,1, ,0,1500,227.079381,-6,-37.536585,
main-20_46.log:2017Apr09-20:47:35:038 | INFO | ,CSV,2017-04-09 20:47:35.031,-1228750296,0.000000,47.592780,-122.382867,26.860000,0.376000,0,1,1, ,0,1500,224.991813,-6,-37.536585,
main-20_46.log:2017Apr09-20:47:35:537 | INFO | ,CSV,2017-04-09 20:47:35.533,-1228750296,0.000000,47.592780,-122.382868,26.860000,0.125000,0,1,1, ,0,1500,225.615161,-6,-37.536585,
main-20_46.log:2017Apr09-20:47:36:045 | INFO | ,CSV,2017-04-09 20:47:36.036,-1228750296,0.000000,47.592780,-122.382868,29.630000,0.350000,0,1,1, ,0,1500,226.583408,-6,-37.536585,
main-20_46.log:2017Apr09-20:47:36:544 | INFO | ,CSV,2017-04-09 20:47:36.538,-1228750296,0.000000,47.592777,-122.382870,29.630000,0.391000,0,1,1, ,0,1500,224.332784,-6,-37.536585,
main-20_46.log:2017Apr09-20:47:37:046 | INFO | ,CSV,2017-04-09 20:47:37.041,-1228750296,0.000000,47.592777,-122.382870,32.590000,0.314000,0,1,1, ,0,1500,226.142759,-6,-37.536585,
main-20_46.log:2017Apr09-20:47:37:546 | INFO | ,CSV,2017-04-09 20:47:37.542,-1228750296,0.000000,47.592780,-122.382870,32.590000,0.371000,0,1,1, ,0,1500,225.309465,-6,-37.536585,
main-20_46.log:2017Apr09-20:47:38:048 | INFO | ,CSV,2017-04-09 20:47:38.044,-1228750296,0.000000,47.592780,-122.382870,34.970000,0.288000,0,1,1, ,0,1500,225.243167,-6,-37.536585,
main-20_46.log:2017Apr09-20:47:38:558 | INFO | ,CSV,2017-04-09 20:47:38.547,-1228750296,0.000000,47.592778,-122.382873,34.970000,0.312000,0,1,1, ,0,1500,224.036519,-6,-37.536585,
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

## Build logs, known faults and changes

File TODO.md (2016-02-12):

# Hackerboat TODO v0.2

## Documentation

* ~~**Create system description document**~~
* ~~**Create controls specification**~~ -- Done to v0.2 requirements
* ~~**Create overall wiring schematic**~~ Done
* ~~**Move all documentation/code/designs to single GitHub repository**~~

## Operations

* ~~**Create launching cradle/sling**~~ -- superseded by events
* ~~**Designate a safety officer**~~ -- 3ric volunteered to take this on
* **Prepare launch & recovery plan** 
* **Provide shade for shore station operator**

## Structure

*  ~~**Fabricate & install solid battery mounts**~~ 
* **Do weight and balance calculations** -- PN noted that since we verified that the boat floated flat and level without the batteries and keel, we can probably just get away with doing the keel plus batteries for now. 
* ~~**Finish keel and add ballast bulbs**~~ -- Alex assembled these. They just need to be filled with rebar. 
* ~~**Add keying to hatches**~~

## Electrical

* ~~**Replace external wiring for motor with stranded wire**~~
* ~~**Re-work antenna**~~
* ~~**Replace servo wiring**~~
* ~~**Add cutoff & enable switches**~~
* ~~**Add mode lights aft**~~
* ~~**Finalize assembly of control & relay boxes**~~ 
* ~~**Functional test of control & relay boxes**~~
* ~~**Improved control box mounting, esp wrt compass heading**~~

## Comms

* ~~**Finalize radio box installation**~~
* ~~**End to end comms test**~~
 
## Controls

* **Debug QGroundControl & our code such that mode switching (especially halt) works reliably without crashing**
* **Add manual steering mode (direct rudder control)** -- Added to Arduino code
* **Add throttle & reverse control** -- Added to Arduino code
* **Get GPS parsing & navigation working correctly**
* **Reduced gear ratio on steering servo** Need to order the parts
* **Add basic startup test (is voltage good? radio good? GPS good?)** -- Specified, implemented on the Arduino only
* **Monitor & report switch & voltage feedback already installed** -- Specified, not yet implemented.

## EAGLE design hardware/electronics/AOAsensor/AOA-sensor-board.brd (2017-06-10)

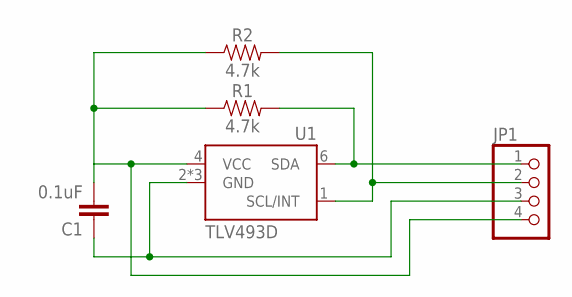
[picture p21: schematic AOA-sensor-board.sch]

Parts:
C1: 0.1uF; 0603
JP1: PINHD-1X4; 1X04
R1, R2: 4.7k; 0603
U1: TLV493D; TSOP-6

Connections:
GND: C1.1, JP1.3, U1.2 (GND), U1.3 (GND), U1.5 (GND)
SCL: JP1.2, R2.2, U1.1 (SCL/INT)
SDA: JP1.1, R1.2, U1.6 (SDA)
VCC: C1.2, JP1.4, R1.1, R2.1, U1.4 (VCC)

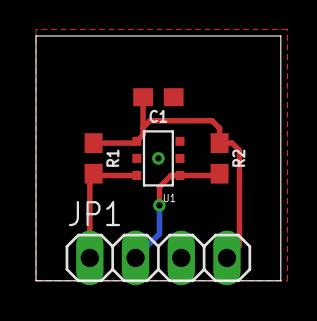
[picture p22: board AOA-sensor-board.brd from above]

Board: 2 copper layers, 13.6 x 13.6 mm, 5 parts (0 on the bottom side), 4 nets.

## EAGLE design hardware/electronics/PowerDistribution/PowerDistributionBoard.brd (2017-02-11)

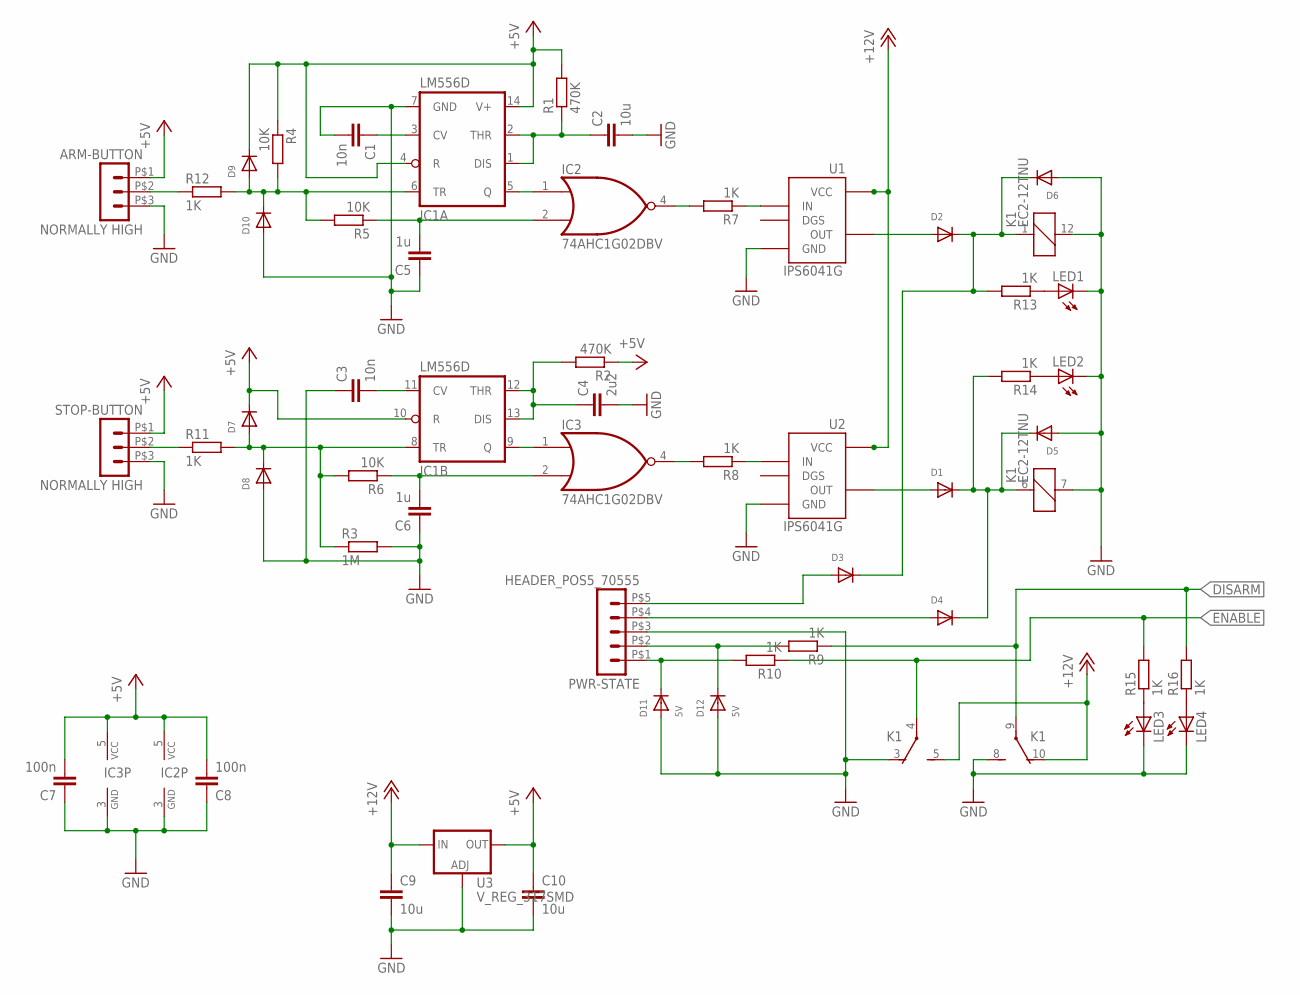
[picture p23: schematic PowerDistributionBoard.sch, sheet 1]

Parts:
ARM-BUTTON: NORMALLY HIGH; 70555-POS3; PARTNO 0705550037
C1, C3: 10n; C0603; PARTNO CL10B103KB8NCNC
C2: 10u; C0603; PARTNO C1608JB1E106M080AC
C4: 2u2; C0603; PARTNO TMK107ABJ225KA-T
C5, C6: 1u; C0603; PARTNO UMK107BJ105KA-T
C7, C8: 100n; C0603; PARTNO CC0603ZRY5V9BB104
C9, C10: 10u; C1206; PARTNO C3216X5R1E106M
D1, D2, D3, D4, D5, D6, D7, D8, D9, D10: DIODESOD-123; SOD-123; PARTNO CDBW140-G
D11, D12: 5V; SOD-123; PARTNO SMF5.0A
IC1: LM556D; SO14; PARTNO LM556CM
IC2, IC3: 74AHC1G02DBV; SOT23-5; PARTNO SN74AHC1G02DBVR
K1: EC2-12TNU; EC2-*TNU; PARTNO EC2-12TNU
LED1, LED2, LED3, LED4: LEDCHIP-LED0805; CHIP-LED0805; PARTNO LG R971-KN-1
PWR-STATE: HEADER_POS5_70555; 70555-POS5; PARTNO 0705550039
R1, R2: 470K; R0603; PARTNO MCR03FZPEJ474
R3: 1M; R0603; PARTNO MCT06030C1004FP500
R4, R5, R6: 10K; R0603; PARTNO RMCF0603FT10K0
R7, R8, R9, R10, R11, R12, R13, R14, R15, R16: 1K; R0603; PARTNO RMCF0603FT1K00
STOP-BUTTON: NORMALLY HIGH; 70555-POS3; PARTNO 0705550037
U1, U2: IPS6041G; SO08; PARTNO IPS6041GPBF
U3: V_REG_317SMD; SOT223; PARTNO NCP1117ST50T3G

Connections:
+5V: ARM-BUTTON.P$1 (1), C7.2, C8.2, C10.1, D7.C, D9.C, IC1.4 (R), IC1.10 (R), IC1.14 (V+), IC2.5 (VCC), IC3.5 (VCC), R1.2, R2.1, R4.1, STOP-BUTTON.P$1 (1), U3.2 (OUT)
+12V: C9.1, K1.5 (S), K1.10 (O), U1.5 (VCC), U1.6 (VCC), U1.7 (VCC), U1.8 (VCC), U2.5 (VCC), U2.6 (VCC), U2.7 (VCC), U2.8 (VCC), U3.3 (IN); also elsewhere on the board
DISARM: K1.9, R9.1, R16.2
ENABLE: K1.4, R10.1, R15.2; also elsewhere on the board
GND: ARM-BUTTON.P$3 (3), C1.2, C2.2, C3.1, C4.2, C5.1, C6.1, C7.1, C8.1, C9.2, C10.2, D5.A, D6.A, D8.A, D10.A, D11.A, D12.A, IC1.7 (GND), IC2.3 (GND), IC3.3 (GND), K1.3 (O), K1.7 (2), K1.8 (S), K1.12 (2), LED1.C, LED2.C, LED3.C, LED4.C, PWR-STATE.P$3 (3), R3.2, STOP-BUTTON.P$3 (3), U1.1 (GND), U2.1 (GND), U3.1 (ADJ); also elsewhere on the board
unnamed: C5.2, IC2.2 (I1), R5.1
unnamed: C1.1, IC1.3 (CV)
unnamed: C6.2, IC3.2 (I1), R6.1
unnamed: C2.1, IC1.1 (DIS), IC1.2 (THR), R1.1
unnamed: C4.1, IC1.12 (THR), IC1.13 (DIS), R2.2
unnamed: IC2.4 (O), R7.2
unnamed: IC1.5 (Q), IC2.1 (I0)
unnamed: D9.A, D10.C, IC1.6 (TR), R4.2, R5.2, R12.2
unnamed: C3.2, IC1.11 (CV)
unnamed: IC3.4 (O), R8.2
unnamed: IC1.9 (Q), IC3.1 (I0)
unnamed: D7.A, D8.C, IC1.8 (TR), R3.1, R6.2, R11.2
unnamed: R7.1, U1.2 (IN)
unnamed: R8.1, U2.2 (IN)
unnamed: D4.A, PWR-STATE.P$4 (4)
unnamed: D3.A, PWR-STATE.P$5 (5)
unnamed: D1.A, U2.4 (OUT)
unnamed: D2.A, U1.4 (OUT)
unnamed: D2.C, D3.C, D6.C, K1.1, R13.2
unnamed: D1.C, D4.C, D5.C, K1.6 (1), R14.2
unnamed: LED2.A, R14.1
unnamed: LED1.A, R13.1
unnamed: D12.C, PWR-STATE.P$2 (2), R9.2
unnamed: D11.C, PWR-STATE.P$1 (1), R10.2
unnamed: ARM-BUTTON.P$2 (2), R12.1
unnamed: R11.1, STOP-BUTTON.P$2 (2)
unnamed: LED3.A, R15.1
unnamed: LED4.A, R16.1

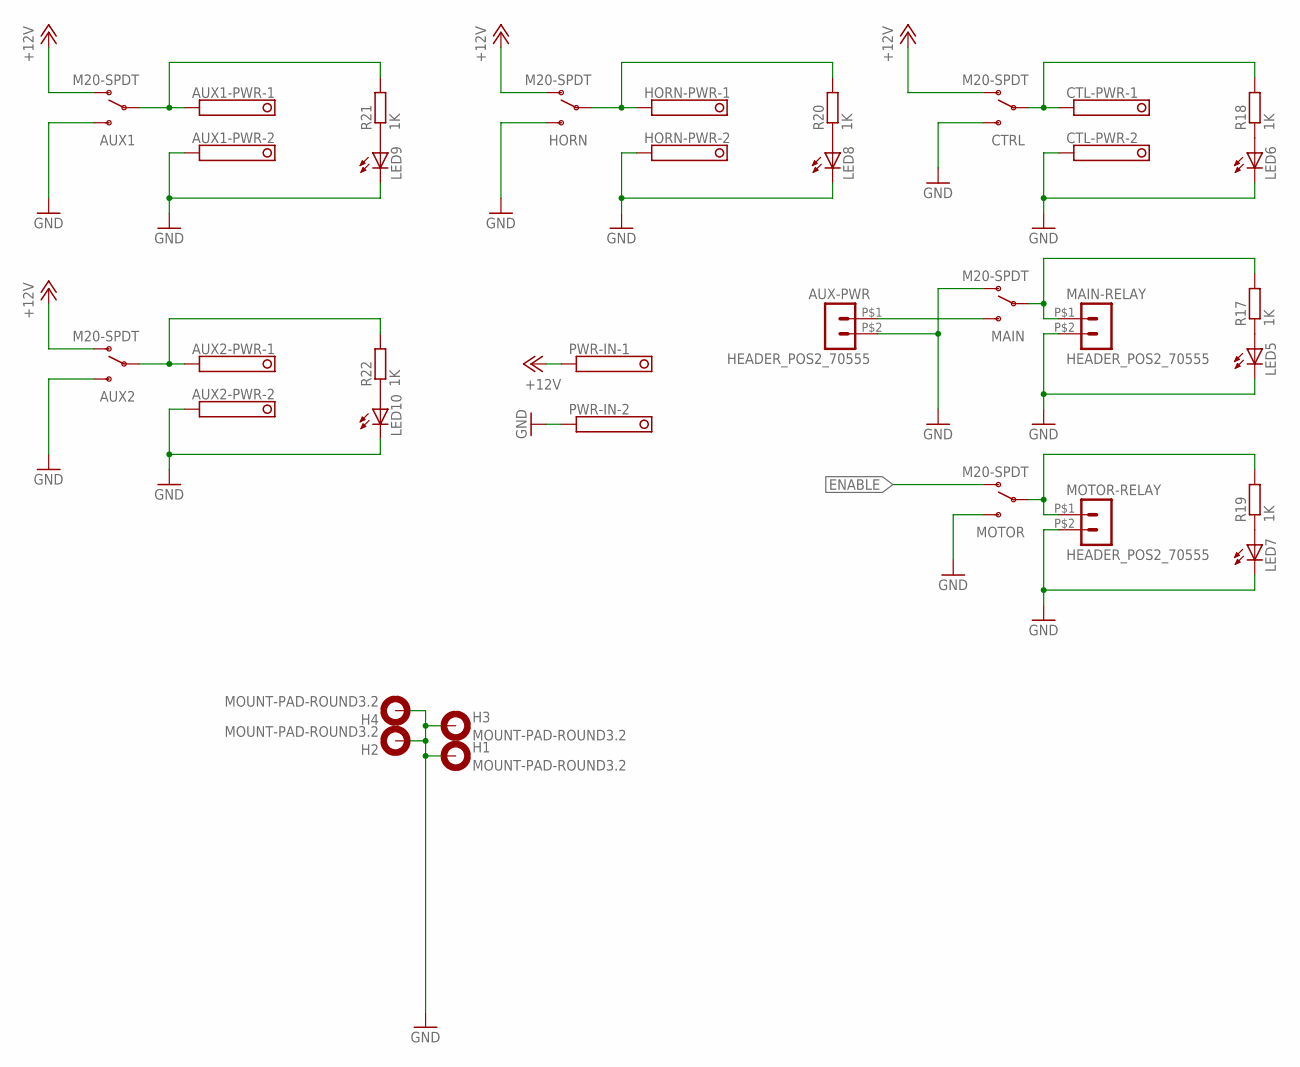
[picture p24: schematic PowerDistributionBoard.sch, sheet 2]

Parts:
AUX1, AUX2: M20-SPDT; PARTNO M2012LL1W01
AUX1-PWR, AUX2-PWR: 1751248; PARTNO 1751248
AUX-PWR: HEADER_POS2_70555; 70555-POS2; PARTNO 0705550036
CTL-PWR: 1751248; PARTNO 1751248
CTRL: M20-SPDT; PARTNO M2012LL1W01
H1, H2, H3, H4: MOUNT-PAD-ROUND3.2; 3,2-PAD
HORN: M20-SPDT; PARTNO M2012LL1W01
HORN-PWR: 1751248; PARTNO 1751248
LED5, LED6, LED7, LED8, LED9, LED10: LEDCHIP-LED0805; CHIP-LED0805; PARTNO LG R971-KN-1
MAIN: M20-SPDT; PARTNO M2012LL1W01
MAIN-RELAY: HEADER_POS2_70555; 70555-POS2; PARTNO 0705550036
MOTOR: M20-SPDT; PARTNO M2012LL1W01
MOTOR-RELAY: HEADER_POS2_70555; 70555-POS2; PARTNO 0705550036
PWR-IN: 1751248; PARTNO 1751248
R17, R18, R19, R20, R21, R22: 1K; R0603; PARTNO RMCF0603FT1K00

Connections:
+12V: AUX1.1 (O), AUX2.1 (O), CTRL.1 (O), HORN.1 (O), PWR-IN.1; also elsewhere on the board
ENABLE: MOTOR.1 (O); also elsewhere on the board
GND: AUX1.3 (S), AUX1-PWR.2, AUX2.3 (S), AUX2-PWR.2, AUX-PWR.P$2 (2), CTL-PWR.2, CTRL.3 (S), H1.B3,2, H2.B3,2, H3.B3,2, H4.B3,2, HORN.3 (S), HORN-PWR.2, LED5.C, LED6.C, LED7.C, LED8.C, LED9.C, LED10.C, MAIN.1 (O), MAIN-RELAY.P$2 (2), MOTOR.3 (S), MOTOR-RELAY.P$2 (2), PWR-IN.2; also elsewhere on the board
unnamed: AUX1.2, AUX1-PWR.1, R21.2
unnamed: LED6.A, R18.1
unnamed: LED9.A, R21.1
unnamed: LED5.A, R17.1
unnamed: HORN.2, HORN-PWR.1, R20.2
unnamed: AUX-PWR.P$1 (1), MAIN.3 (S)
unnamed: LED7.A, R19.1
unnamed: MOTOR.2, MOTOR-RELAY.P$1 (1), R19.2
unnamed: AUX2.2, AUX2-PWR.1, R22.2
unnamed: CTL-PWR.1, CTRL.2, R18.2
unnamed: LED10.A, R22.1
unnamed: LED8.A, R20.1
unnamed: MAIN.2, MAIN-RELAY.P$1 (1), R17.2

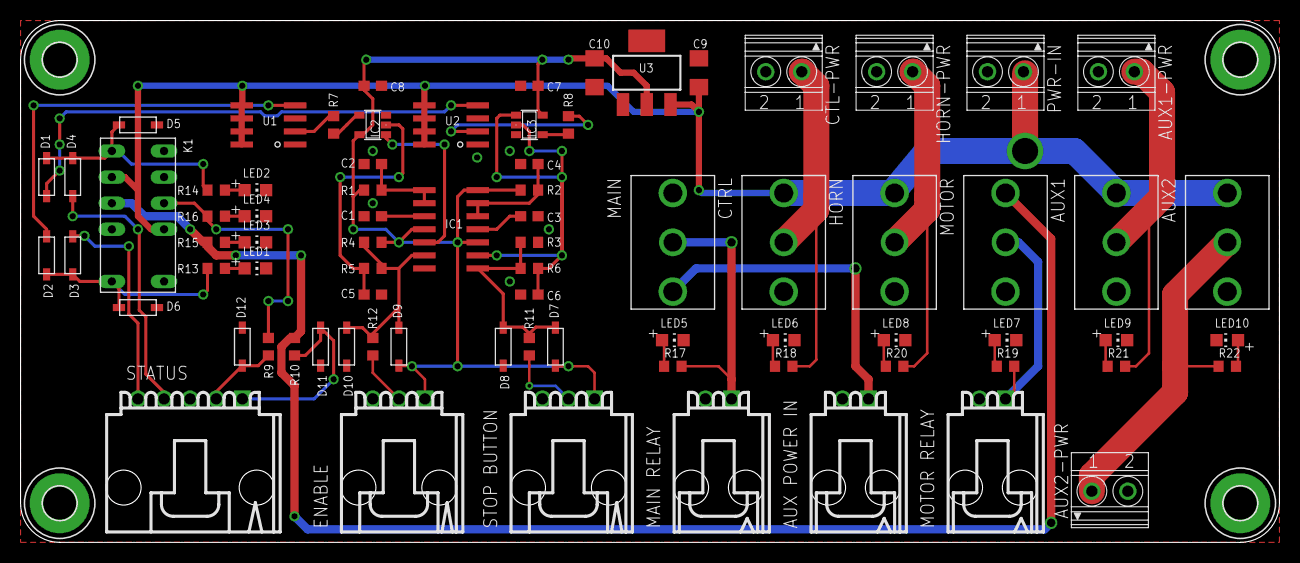
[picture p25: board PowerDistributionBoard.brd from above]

Board: 2 copper layers, 122.6 x 50.8 mm, 82 parts (0 on the bottom side), 46 nets.

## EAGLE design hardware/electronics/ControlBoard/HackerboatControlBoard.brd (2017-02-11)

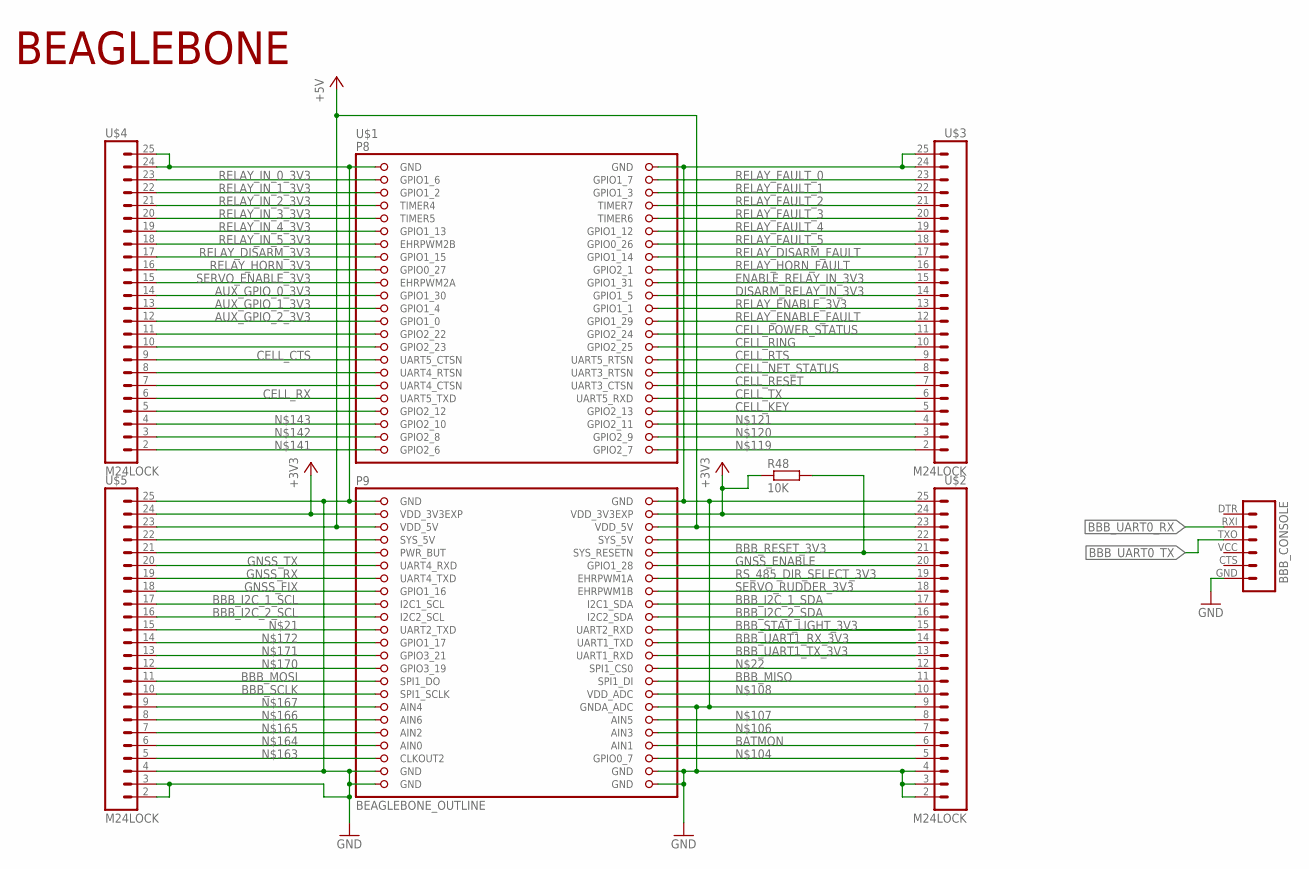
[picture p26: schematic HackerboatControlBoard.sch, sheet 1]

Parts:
BBB_CONSOLE: FTDI_BASICPTH; FTDI_BASIC; PARTNO 215299-6
R48: 10K; R0603; PARTNO RNCP0603FTD10K0
U$1: BEAGLEBONE_OUTLINE; BEAGLEBONE_SHIELD; PARTNO ?
U$2, U$3, U$4, U$5: M24LOCK; 1X24_LOCK; PARTNO *

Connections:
+3V3: R48.1, U$1.49 (VDD_3V3EXP), U$1.50 (VDD_3V3EXP), U$2.24, U$5.24; also elsewhere on the board
+5V: U$1.51 (VDD_5V), U$1.52 (VDD_5V), U$2.23, U$5.23; also elsewhere on the board
AUX_GPIO_0_3V3: U$1.21 (GPIO1_30), U$4.14; also elsewhere on the board
AUX_GPIO_1_3V3: U$1.23 (GPIO1_4), U$4.13; also elsewhere on the board
AUX_GPIO_2_3V3: U$1.25 (GPIO1_0), U$4.12; also elsewhere on the board
BATMON: U$1.86 (AIN1), U$2.6; also elsewhere on the board
BBB_I2C_1_SCL: U$1.63 (I2C1_SCL), U$5.17; also elsewhere on the board
BBB_I2C_1_SDA: U$1.64 (I2C1_SDA), U$2.17; also elsewhere on the board
BBB_I2C_2_SCL: U$1.65 (I2C2_SCL), U$5.16; also elsewhere on the board
BBB_I2C_2_SDA: U$1.66 (I2C2_SDA), U$2.16; also elsewhere on the board
BBB_MISO: U$1.76 (SPI1_DI), U$2.11; also elsewhere on the board
BBB_MOSI: U$1.75 (SPI1_DO), U$5.11; also elsewhere on the board
BBB_RESET_3V3: R48.2, U$1.56 (SYS_RESETN), U$2.21; also elsewhere on the board
BBB_SCLK: U$1.77 (SPI1_SCLK), U$5.10; also elsewhere on the board
BBB_STAT_LIGHT_3V3: U$1.68 (UART2_RXD), U$2.15
BBB_UART0_RX: BBB_CONSOLE.RXI (2); also elsewhere on the board
BBB_UART0_TX: BBB_CONSOLE.TXO (3); also elsewhere on the board
BBB_UART1_RX_3V3: U$1.70 (UART1_TXD), U$2.14; also elsewhere on the board
BBB_UART1_TX_3V3: U$1.72 (UART1_RXD), U$2.13; also elsewhere on the board
CELL_CTS: U$1.31 (UART5_CTSN), U$4.9; also elsewhere on the board
CELL_KEY: U$1.40 (GPIO2_13), U$3.5; also elsewhere on the board
CELL_NET_STATUS: U$1.34 (UART3_RTSN), U$3.8; also elsewhere on the board
CELL_POWER_STATUS: U$1.28 (GPIO2_24), U$3.11; also elsewhere on the board
CELL_RESET: U$1.36 (UART3_CTSN), U$3.7; also elsewhere on the board
CELL_RING: U$1.30 (GPIO2_25), U$3.10; also elsewhere on the board
CELL_RTS: U$1.32 (UART5_RTSN), U$3.9; also elsewhere on the board
CELL_RX: U$1.37 (UART5_TXD), U$4.6; also elsewhere on the board
CELL_TX: U$1.38 (UART5_RXD), U$3.6; also elsewhere on the board
DISARM_RELAY_IN_3V3: U$1.22 (GPIO1_5), U$3.14; also elsewhere on the board
ENABLE_RELAY_IN_3V3: U$1.20 (GPIO1_31), U$3.15; also elsewhere on the board
GND: BBB_CONSOLE.GND (6), U$1.1 (GND), U$1.2 (GND), U$1.47 (GND), U$1.48 (GND), U$1.80 (GNDA_ADC), U$1.89 (GND), U$1.90 (GND), U$1.91 (GND), U$1.92 (GND), U$2.2, U$2.3, U$2.4, U$2.9, U$2.25, U$3.24, U$3.25, U$4.24, U$4.25, U$5.2, U$5.3, U$5.4, U$5.25; also elsewhere on the board
GNSS_ENABLE: U$1.58 (GPIO1_28), U$2.20; also elsewhere on the board
GNSS_FIX: U$1.61 (GPIO1_16), U$5.18; also elsewhere on the board
GNSS_RX: U$1.59 (UART4_TXD), U$5.19; also elsewhere on the board
GNSS_TX: U$1.57 (UART4_RXD), U$5.20; also elsewhere on the board
unnamed: U$1.67 (UART2_TXD), U$5.15
unnamed: U$1.74 (SPI1_CS0), U$2.12
unnamed: U$1.27 (GPIO2_22), U$4.11
unnamed: U$1.29 (GPIO2_23), U$4.10
unnamed: U$1.33 (UART4_RTSN), U$4.8
unnamed: U$1.35 (UART4_CTSN), U$4.7
unnamed: U$1.39 (GPIO2_12), U$4.5
unnamed: U$1.88 (GPIO0_7), U$2.5
unnamed: U$1.84 (AIN3), U$2.7
unnamed: U$1.82 (AIN5), U$2.8
unnamed: U$1.78 (VDD_ADC), U$2.10
unnamed: U$1.54 (SYS_5V), U$2.22
unnamed: U$1.46 (GPIO2_7), U$3.2
unnamed: U$1.44 (GPIO2_9), U$3.3
unnamed: U$1.42 (GPIO2_11), U$3.4
unnamed: U$1.45 (GPIO2_6), U$4.2
unnamed: U$1.43 (GPIO2_8), U$4.3
unnamed: U$1.41 (GPIO2_10), U$4.4
unnamed: U$1.87 (CLKOUT2), U$5.5
unnamed: U$1.85 (AIN0), U$5.6
unnamed: U$1.83 (AIN2), U$5.7
unnamed: U$1.81 (AIN6), U$5.8
unnamed: U$1.79 (AIN4), U$5.9
unnamed: U$1.73 (GPIO3_19), U$5.12
unnamed: U$1.71 (GPIO3_21), U$5.13
unnamed: U$1.69 (GPIO1_17), U$5.14
unnamed: U$1.55 (PWR_BUT), U$5.21
RELAY_DISARM_3V3: U$1.15 (GPIO1_15), U$4.17; also elsewhere on the board
RELAY_DISARM_FAULT: U$1.16 (GPIO1_14), U$3.17; also elsewhere on the board
RELAY_ENABLE_3V3: U$1.24 (GPIO1_1), U$3.13; also elsewhere on the board
RELAY_ENABLE_FAULT: U$1.26 (GPIO1_29), U$3.12; also elsewhere on the board
RELAY_FAULT_0: U$1.4 (GPIO1_7), U$3.23; also elsewhere on the board
RELAY_FAULT_1: U$1.6 (GPIO1_3), U$3.22; also elsewhere on the board
RELAY_FAULT_2: U$1.8 (TIMER7), U$3.21; also elsewhere on the board
RELAY_FAULT_3: U$1.10 (TIMER6), U$3.20; also elsewhere on the board
RELAY_FAULT_4: U$1.12 (GPIO1_12), U$3.19; also elsewhere on the board
RELAY_FAULT_5: U$1.14 (GPIO0_26), U$3.18; also elsewhere on the board
RELAY_HORN_3V3: U$1.17 (GPIO0_27), U$4.16; also elsewhere on the board
RELAY_HORN_FAULT: U$1.18 (GPIO2_1), U$3.16; also elsewhere on the board
RELAY_IN_0_3V3: U$1.3 (GPIO1_6), U$4.23; also elsewhere on the board
RELAY_IN_1_3V3: U$1.5 (GPIO1_2), U$4.22; also elsewhere on the board
RELAY_IN_2_3V3: U$1.7 (TIMER4), U$4.21; also elsewhere on the board
RELAY_IN_3_3V3: U$1.9 (TIMER5), U$4.20; also elsewhere on the board
RELAY_IN_4_3V3: U$1.11 (GPIO1_13), U$4.19; also elsewhere on the board
RELAY_IN_5_3V3: U$1.13 (EHRPWM2B), U$4.18; also elsewhere on the board
RS_485_DIR_SELECT_3V3: U$1.60 (EHRPWM1A), U$2.19; also elsewhere on the board
SERVO_ENABLE_3V3: U$1.19 (EHRPWM2A), U$4.15; also elsewhere on the board
SERVO_RUDDER_3V3: U$1.62 (EHRPWM1B), U$2.18; also elsewhere on the board
SYS_5V: U$1.53 (SYS_5V), U$5.22

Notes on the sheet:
BEAGLEBONE

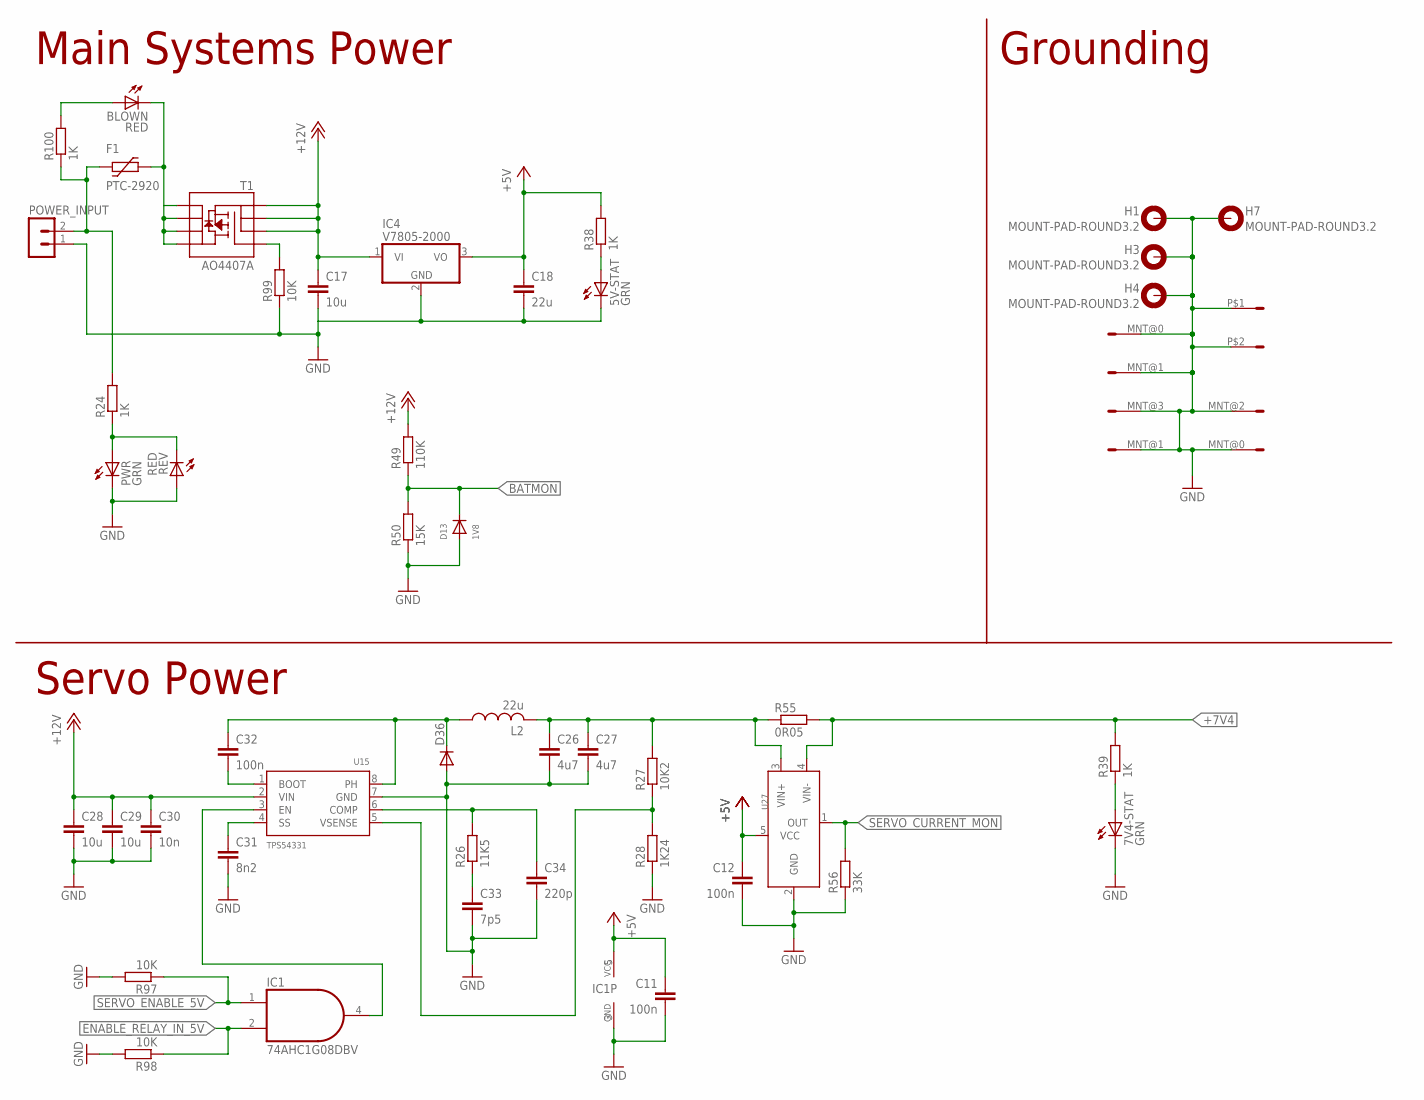
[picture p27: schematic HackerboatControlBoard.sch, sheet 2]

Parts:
5V-STAT, 7V4-STAT: GRN; CHIPLED_0805; PARTNO LG R971-KN-1
BLOWN: RED; CHIPLED_0805; PARTNO LH R974-LP-1
C11, C12, C32: 100n; C0603; PARTNO CC0603KRX7R9BB104
C17, C28, C29: 10u; C1210; PARTNO UMK325BJ106MM
C18: 22u; C1210; PARTNO GRM32ER61E226KE15K
C26, C27: 4u7; C1210; PARTNO UMK325F475ZH
C30: 10n; C0603; PARTNO CL10B103KB8NCNC
C31: 8n2; C0603; PARTNO CL10B822KB8SFNC
C33: 7p5; C0603; PARTNO CL10C7R5DB8NNNC
C34: 220p; C0603; PARTNO CL10B221KC8WPNC
CELL: FONA; FONA-3G; PARTNO BCS-118-L-S-TE
D13: 1V8; SOD-123; PARTNO MMSZ4678-TP
D36: SPARKFUN_DIODESMA; SPARKFUN_SMA-DIODE; PARTNO SK310A-LTP
F1: PTC-2920; 2920L; PARTNO MF-LSMF300/24X-2
GPS: ULTIMATE-GPS; PARTNO BCS-109-L-S-TE
H1, H3, H4, H7: MOUNT-PAD-ROUND3.2; 3,2-PAD; PARTNO ?
IC1: 74AHC1G08DBV; SOT23-5; PARTNO MC74HC1G08DTT1G
IC4: V7805-2000; TO220V; PARTNO V7805-2000
IMU: 9-DOF-BREAKOUT; PARTNO BCS-110-L-S-TE
L2: 22u; NR60XX; PARTNO NR6045T220M
POWER_INPUT: 3-1437664-0; CONN-2; PARTNO NC6-P108-02
PWR: GRN; CHIPLED_0805; PARTNO LG R971-KN-1
R24, R38, R39, R100: 1K; R0603; PARTNO RMCF0603FT1K00
R26: 11K5; R0603; PARTNO RC0603FR-0711K5L
R27: 10K2; R0603; PARTNO RC0603FR-0710K2L
R28: 1K24; R0603; PARTNO RC0603FR-071K24L
R49: 110K; R0603; PARTNO RC0603JR-07110KL
R50: 15K; R0603; PARTNO RC0603JR-0715KL
R55: 0R05; R2512; PARTNO PE2512FKE070R05L
R56: 33K; R0603; PARTNO ERJ-3EKF3302V
R97, R98, R99: 10K; R0603; PARTNO RNCP0603FTD10K0
REV: RED; CHIPLED_0805; PARTNO LH R974-LP-1
T1: AO4407A; SO08; PARTNO AO4407A
U15: TPS54331; SO08; PARTNO TPS54331DR
U27: INA169; SOT23-5L; PARTNO INA169NA/3K

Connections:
+5V: C11.1, C12.1, C18.1, IC1.5 (VCC), IC4.3 (VO), R38.2, U27.5 (VCC); also elsewhere on the board
+7V4: R39.2, R55.2, U27.4 (VIN-); also elsewhere on the board
+7V4_OUT: C26.1, C27.1, L2.2, R27.2, R55.1, U27.3 (VIN+)
+12V: C17.1, C28.1, C29.1, C30.1, IC4.1 (VI), R49.2, T1.1 (S), T1.2 (S), T1.3 (S), U15.2 (VIN); also elsewhere on the board
BATMON: D13.C, R49.1, R50.2; also elsewhere on the board
ENABLE_RELAY_IN_5V: IC1.2 (I1), R98.1; also elsewhere on the board
GND: 5V-STAT.C, 7V4-STAT.C, C11.2, C12.2, C17.2, C18.2, C26.2, C27.2, C28.2, C29.2, C30.2, C31.2, C33.2, C34.2, CELL.P$1 (9), CELL.P$2 (9), D13.A, D36.A, GPS.MNT@0 (9), GPS.MNT@1 (9), H1.B3,2, H3.B3,2, H4.B3,2, H7.B3,2, IC1.3 (GND), IC4.2 (GND), IMU.MNT@0 (9), IMU.MNT@1 (9), IMU.MNT@2 (9), IMU.MNT@3 (9), POWER_INPUT.1, PWR.C, R28.1, R50.1, R56.1, R97.2, R98.2, R99.1, REV.A, U15.7 (GND), U27.2 (GND); also elsewhere on the board
unnamed: IC1.4 (O), U15.3 (EN)
unnamed: C31.1, U15.4 (SS)
unnamed: C32.2, U15.1 (BOOT)
unnamed: C32.1, D36.C, L2.1, U15.8 (PH)
unnamed: C33.1, R26.1
unnamed: C34.1, R26.2, U15.6 (COMP)
unnamed: R27.1, R28.2, U15.5 (VSENSE)
unnamed: BLOWN.C, F1.P$2 (2), T1.5 (D), T1.6 (D), T1.7 (D), T1.8 (D)
unnamed: R99.2, T1.4 (G)
unnamed: F1.P$1 (1), POWER_INPUT.2, R24.2, R100.1
unnamed: BLOWN.A, R100.2
unnamed: PWR.A, R24.1, REV.C
unnamed: 5V-STAT.A, R38.1
unnamed: 7V4-STAT.A, R39.1
SERVO_CURRENT_MON: R56.2, U27.1 (OUT); also elsewhere on the board
SERVO_ENABLE_5V: IC1.1 (I0), R97.1; also elsewhere on the board

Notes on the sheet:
Main Systems Power
Servo Power
Grounding

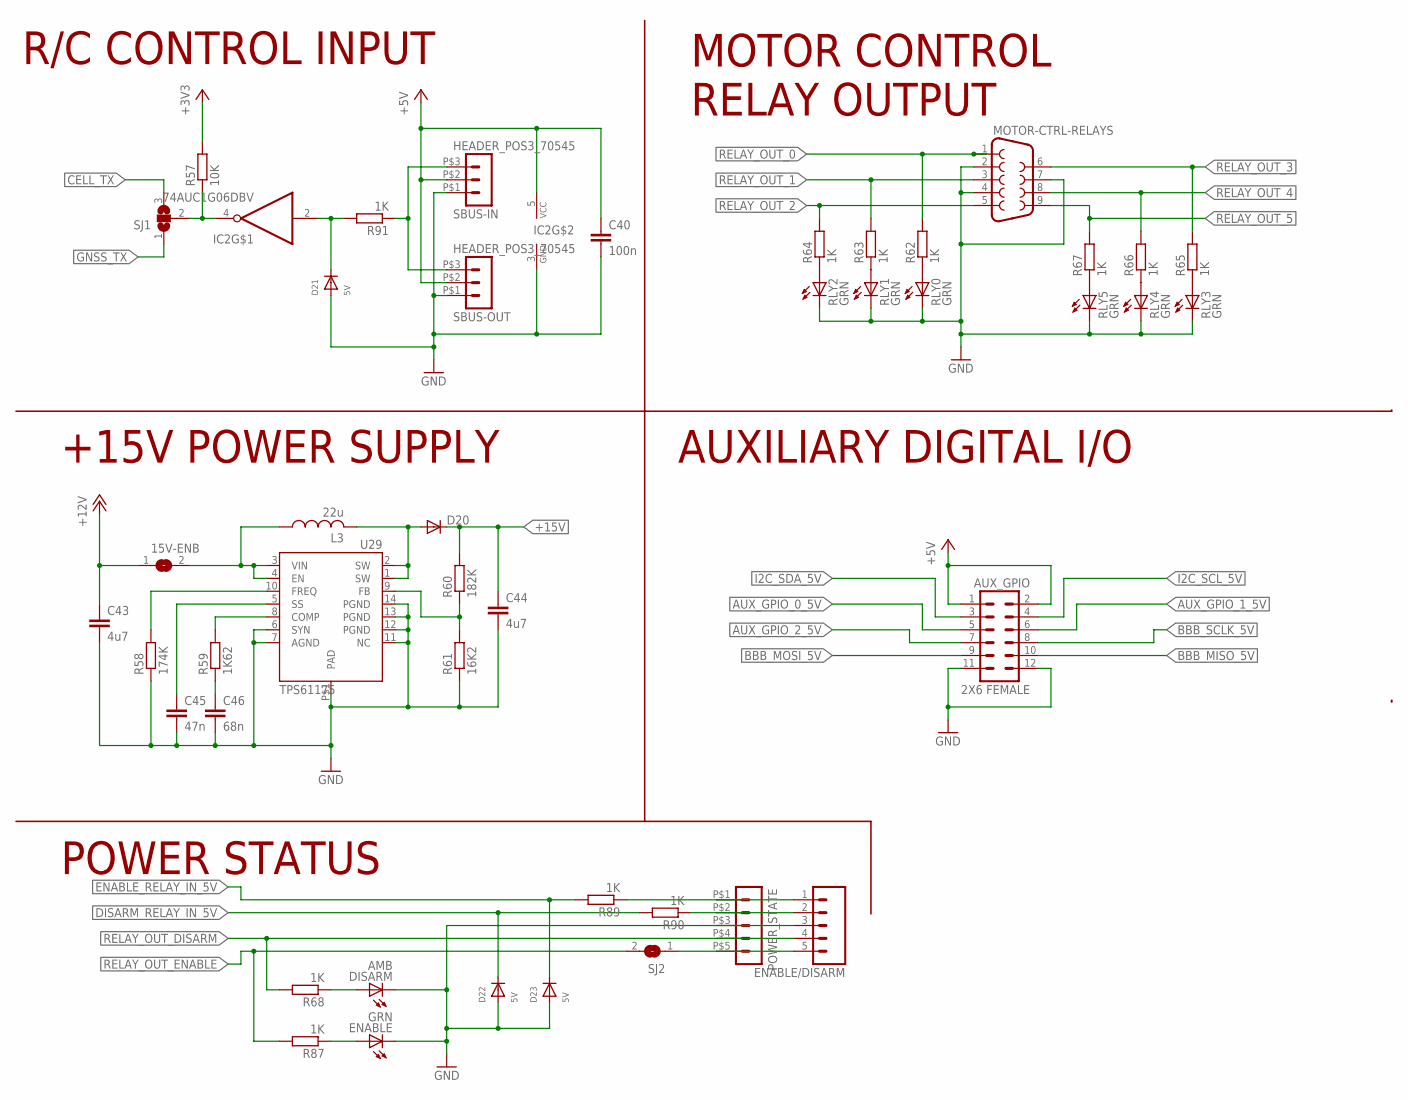
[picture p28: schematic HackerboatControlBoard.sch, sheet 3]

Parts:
15V-ENB: SJ; PARTNO ?
AUX_GPIO: 2X6 FEMALE; 2X6; PARTNO *
C40: 100n; C0603; PARTNO CC0603KRX7R9BB104
C43, C44: 4u7; C1210; PARTNO UMK325F475ZH
C45: 47n; C0603; PARTNO C1608X7R1H473M
C46: 68n; C0603; PARTNO CL10C680JB8NNNC
D20: SPARKFUN_DIODESMA; SPARKFUN_SMA-DIODE; PARTNO SK310A-LTP
D21, D22, D23: 5V; SOD-123; PARTNO SMF5.0A
DISARM: AMB; CHIPLED_0805; PARTNO HSMA-C170
ENABLE: GRN; CHIPLED_0805; PARTNO LG R971-KN-1
ENABLE/DISARM: M05LOCK; 1X05_LOCK; PARTNO *
IC2: 74AUC1G06DBV; SOT23-5; PARTNO SN74LVC1G06DBVR
L3: 22u; SRN8040; PARTNO SRN8040-220M
MOTOR-CTRL-RELAYS: DB9FEMALE; DB9; PARTNO 1734354-1
POWER_STATE: HEADER_POS5_70555; 70555-POS5; PARTNO 0705550039
R57: 10K; R0603; PARTNO RNCP0603FTD10K0
R58: 174K; R0603; PARTNO RC0603FR-07174KL
R59: 1K62; R0603; PARTNO RC0603FR-071K62L
R60: 182K; R0603; PARTNO ERJ-3EKF1823V
R61: 16K2; R0603; PARTNO RC0603FR-0716K2L
R62, R63, R64, R65, R66, R67, R68, R87, R89, R90, R91: 1K; R0603; PARTNO RMCF0603FT1K00
RLY0, RLY1, RLY2, RLY3, RLY4, RLY5: GRN; CHIPLED_0805; PARTNO LG R971-KN-1
SBUS-IN: HEADER_POS3_70545; 70545-POS3; PARTNO 0705450037
SBUS-OUT: HEADER_POS3_70545; 70545-POS3; PARTNO 0705450037
SJ1: SJ2W; SJ_2; PARTNO ?
SJ2: SJ; PARTNO *
U29: TPS61175; HTSSOP14; PARTNO TPS61175PWPR

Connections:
+3V3: R57.2; also elsewhere on the board
+5V: AUX_GPIO.1, AUX_GPIO.2, C40.1, IC2.5 (VCC), SBUS-IN.P$2 (2), SBUS-OUT.P$2 (2); also elsewhere on the board
+12V: 15V-ENB.1, C43.1; also elsewhere on the board
+15V: C44.1, D20.C, R60.2; also elsewhere on the board
AUX_GPIO_0_5V: AUX_GPIO.5; also elsewhere on the board
AUX_GPIO_1_5V: AUX_GPIO.6; also elsewhere on the board
AUX_GPIO_2_5V: AUX_GPIO.7; also elsewhere on the board
BBB_MISO_5V: AUX_GPIO.10; also elsewhere on the board
BBB_MOSI_5V: AUX_GPIO.9; also elsewhere on the board
BBB_SCLK_5V: AUX_GPIO.8; also elsewhere on the board
CELL_TX: SJ1.3; also elsewhere on the board
DISARM_RELAY_IN_5V: D22.C, R90.2; also elsewhere on the board
ENABLE_RELAY_IN_5V: D23.C, R89.2; also elsewhere on the board
GND: AUX_GPIO.11, AUX_GPIO.12, C40.2, C43.2, C44.2, C45.2, C46.2, D21.A, D22.A, D23.A, DISARM.C, ENABLE.C, ENABLE/DISARM.3, IC2.3 (GND), MOTOR-CTRL-RELAYS.2, MOTOR-CTRL-RELAYS.4, MOTOR-CTRL-RELAYS.7, POWER_STATE.P$3 (3), R58.1, R61.1, RLY0.C, RLY1.C, RLY2.C, RLY3.C, RLY4.C, RLY5.C, SBUS-IN.P$1 (1), SBUS-OUT.P$1 (1), U29.6 (SYN), U29.7 (AGND), U29.11 (NC), U29.12 (PGND), U29.13 (PGND), U29.14 (PGND), U29.P$1 (PAD); also elsewhere on the board
GNSS_TX: SJ1.1; also elsewhere on the board
I2C_SCL_5V: AUX_GPIO.4; also elsewhere on the board
I2C_SDA_5V: AUX_GPIO.3; also elsewhere on the board
unnamed: D21.C, IC2.2 (I), R91.2
unnamed: IC2.4 (O), R57.1, SJ1.2
unnamed: R62.1, RLY0.A
unnamed: R63.1, RLY1.A
unnamed: R64.1, RLY2.A
unnamed: DISARM.A, R68.1
unnamed: R65.1, RLY3.A
unnamed: R66.1, RLY4.A
unnamed: R67.1, RLY5.A
unnamed: ENABLE.A, R87.1
unnamed: C46.1, R59.1
unnamed: R59.2, U29.8 (COMP)
unnamed: C45.1, U29.5 (SS)
unnamed: R58.2, U29.10 (FREQ)
unnamed: D20.A, L3.2, U29.1 (SW), U29.2 (SW)
unnamed: R60.1, R61.2, U29.9 (FB)
unnamed: ENABLE/DISARM.1, POWER_STATE.P$1 (1), R89.1
unnamed: ENABLE/DISARM.2, POWER_STATE.P$2 (2), R90.1
unnamed: 15V-ENB.2, L3.1, U29.3 (VIN), U29.4 (EN)
unnamed: ENABLE/DISARM.5, POWER_STATE.P$5 (5), SJ2.1
RELAY_OUT_0: MOTOR-CTRL-RELAYS.1, R62.2; also elsewhere on the board
RELAY_OUT_1: MOTOR-CTRL-RELAYS.3, R63.2; also elsewhere on the board
RELAY_OUT_2: MOTOR-CTRL-RELAYS.5, R64.2; also elsewhere on the board
RELAY_OUT_3: MOTOR-CTRL-RELAYS.6, R65.2; also elsewhere on the board
RELAY_OUT_4: MOTOR-CTRL-RELAYS.8, R66.2; also elsewhere on the board
RELAY_OUT_5: MOTOR-CTRL-RELAYS.9, R67.2; also elsewhere on the board
RELAY_OUT_DISARM: ENABLE/DISARM.4, POWER_STATE.P$4 (4), R68.2; also elsewhere on the board
RELAY_OUT_ENABLE: R87.2, SJ2.2; also elsewhere on the board
SBUS_IN_5V: R91.1, SBUS-IN.P$3 (3), SBUS-OUT.P$3 (3)

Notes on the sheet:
R/C CONTROL INPUT
+15V POWER SUPPLY
MOTOR CONTROL RELAY OUTPUT
AUXILIARY DIGITAL I/O
POWER STATUS

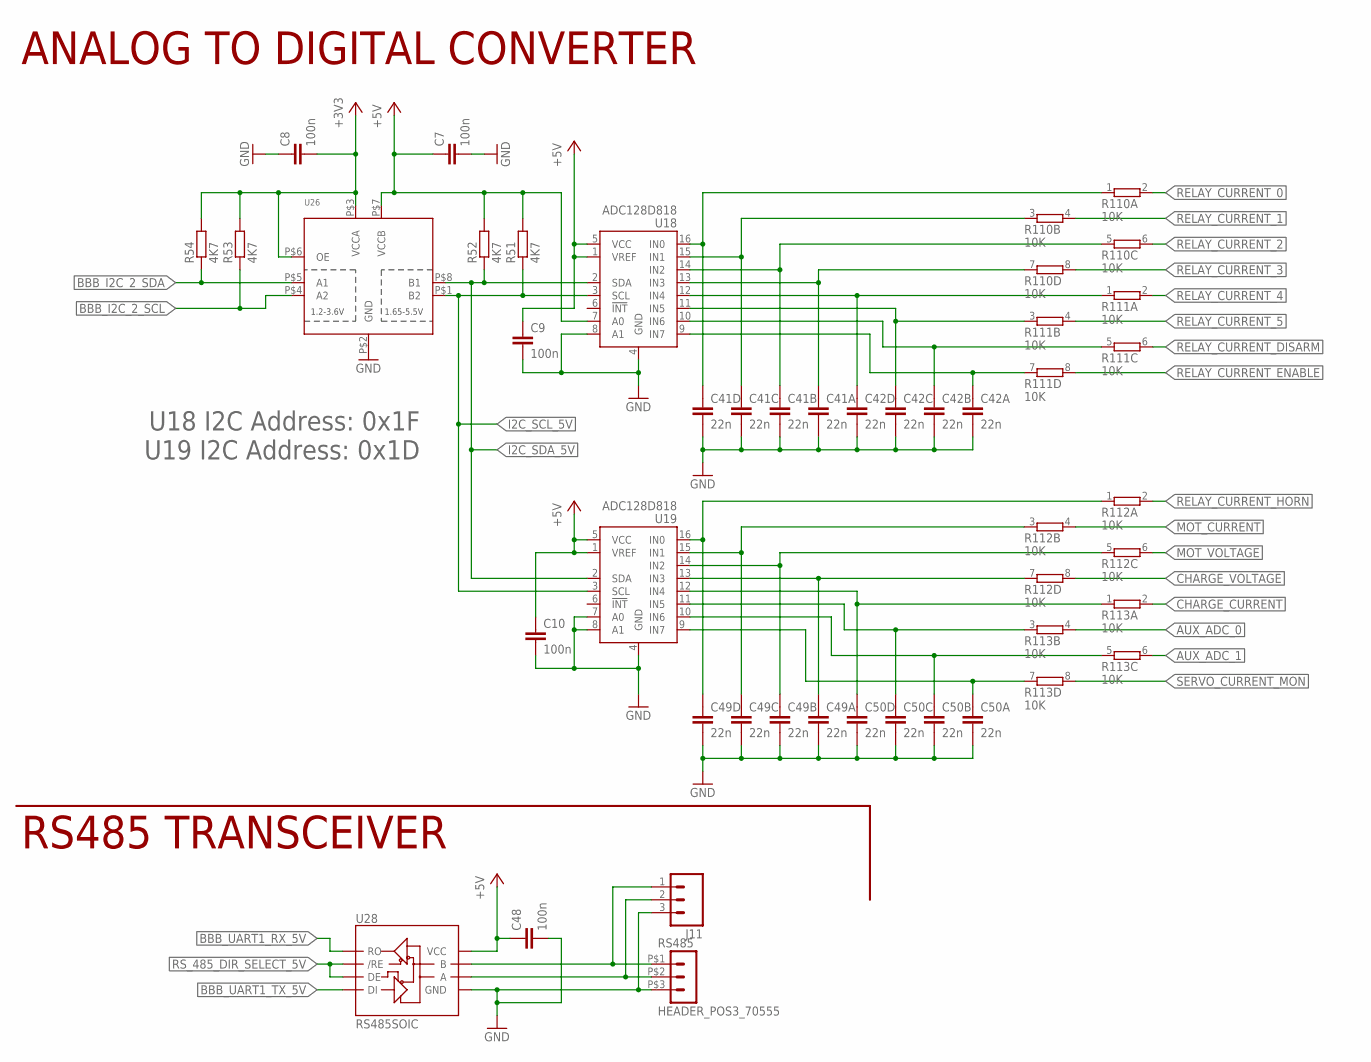
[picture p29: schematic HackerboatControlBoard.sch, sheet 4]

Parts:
C7, C8, C9, C10, C48: 100n; C0603; PARTNO CC0603KRX7R9BB104
C41, C42, C49, C50: 22n; 0805X4-CAP; PARTNO CKCL44X5R1C223M085AA
J11: M03LOCK; 1X03_LOCK; PARTNO ?
R51, R52, R53, R54: 4K7; R0603; PARTNO RC1608J472CS
R110, R111, R112, R113: 10K; CTS742C083-RES; PARTNO 742C083103JPTR
RS485: HEADER_POS3_70555; 70555-POS3; PARTNO 0705550037
U18, U19: ADC128D818; TSSOP16; PARTNO ADC128D818CIMTX
U26: TXS0102; VFSOP-8; PARTNO TXS0102DCURG4
U28: RS485SOIC; SO08; PARTNO SN75176BDR

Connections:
+3V3: C8.2, R53.2, R54.2, U26.P$3 (VCCA), U26.P$6 (OE); also elsewhere on the board
+5V: C7.1, C9.1, C10.1, C48.1, R51.2, R52.2, U18.1 (VREF), U18.5 (VCC), U18.7 (A0), U19.1 (VREF), U19.5 (VCC), U26.P$7 (VCCB), U28.8 (VCC); also elsewhere on the board
AUX_ADC_0: R113.4 (2); also elsewhere on the board
AUX_ADC_1: R113.6 (2); also elsewhere on the board
BBB_I2C_2_SCL: R53.1, U26.P$4 (A2); also elsewhere on the board
BBB_I2C_2_SDA: R54.1, U26.P$5 (A1); also elsewhere on the board
BBB_UART1_RX_5V: U28.1 (RO); also elsewhere on the board
BBB_UART1_TX_5V: U28.4 (DI); also elsewhere on the board
CHARGE_CURRENT: R113.2; also elsewhere on the board
CHARGE_VOLTAGE: R112.8 (2); also elsewhere on the board
GND: C7.2, C8.1, C9.2, C10.2, C41.2, C41.4 (2), C41.6 (2), C41.8 (2), C42.2, C42.4 (2), C42.6 (2), C42.8 (2), C48.2, C49.2, C49.4 (2), C49.6 (2), C49.8 (2), C50.2, C50.4 (2), C50.6 (2), C50.8 (2), J11.3, RS485.P$3 (3), U18.4 (GND), U18.8 (A1), U19.4 (GND), U19.7 (A0), U19.8 (A1), U26.P$2 (GND), U28.5 (GND); also elsewhere on the board
I2C_SCL_5V: R51.1, U18.3 (SCL), U19.3 (SCL), U26.P$1 (B2); also elsewhere on the board
I2C_SDA_5V: R52.1, U18.2 (SDA), U19.2 (SDA), U26.P$8 (B1); also elsewhere on the board
MOT_CURRENT: R112.4 (2); also elsewhere on the board
MOT_VOLTAGE: R112.6 (2); also elsewhere on the board
unnamed: J11.1, RS485.P$1 (1), U28.7 (B)
unnamed: J11.2, RS485.P$2 (2), U28.6 (A)
unnamed: C41.7 (1), R110.1, U18.16 (IN0)
unnamed: C41.5 (1), R110.3 (1), U18.15 (IN1)
unnamed: C49.7 (1), R112.1, U19.16 (IN0)
unnamed: C41.3 (1), R110.5 (1), U18.14 (IN2)
unnamed: C41.1, R110.7 (1), U18.13 (IN3)
unnamed: C42.7 (1), R111.1, U18.12 (IN4)
unnamed: C42.5 (1), R111.3 (1), U18.11 (IN5)
unnamed: C42.3 (1), R111.5 (1), U18.10 (IN6)
unnamed: C42.1, R111.7 (1), U18.9 (IN7)
unnamed: C49.5 (1), R112.3 (1), U19.15 (IN1)
unnamed: C49.3 (1), R112.5 (1), U19.14 (IN2)
unnamed: C49.1, R112.7 (1), U19.13 (IN3)
unnamed: C50.7 (1), R113.1, U19.12 (IN4)
unnamed: C50.5 (1), R113.3 (1), U19.11 (IN5)
unnamed: C50.3 (1), R113.5 (1), U19.10 (IN6)
unnamed: C50.1, R113.7 (1), U19.9 (IN7)
RELAY_CURRENT_0: R110.2; also elsewhere on the board
RELAY_CURRENT_1: R110.4 (2); also elsewhere on the board
RELAY_CURRENT_2: R110.6 (2); also elsewhere on the board
RELAY_CURRENT_3: R110.8 (2); also elsewhere on the board
RELAY_CURRENT_4: R111.2; also elsewhere on the board
RELAY_CURRENT_5: R111.4 (2); also elsewhere on the board
RELAY_CURRENT_DISARM: R111.6 (2); also elsewhere on the board
RELAY_CURRENT_ENABLE: R111.8 (2); also elsewhere on the board
RELAY_CURRENT_HORN: R112.2; also elsewhere on the board
RS_485_DIR_SELECT_5V: U28.2 (/RE), U28.3 (DE); also elsewhere on the board
SERVO_CURRENT_MON: R113.8 (2); also elsewhere on the board

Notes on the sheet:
ANALOG TO DIGITAL CONVERTER
RS485 TRANSCEIVER
U18 I2C Address: 0x1F U19 I2C Address: 0x1D

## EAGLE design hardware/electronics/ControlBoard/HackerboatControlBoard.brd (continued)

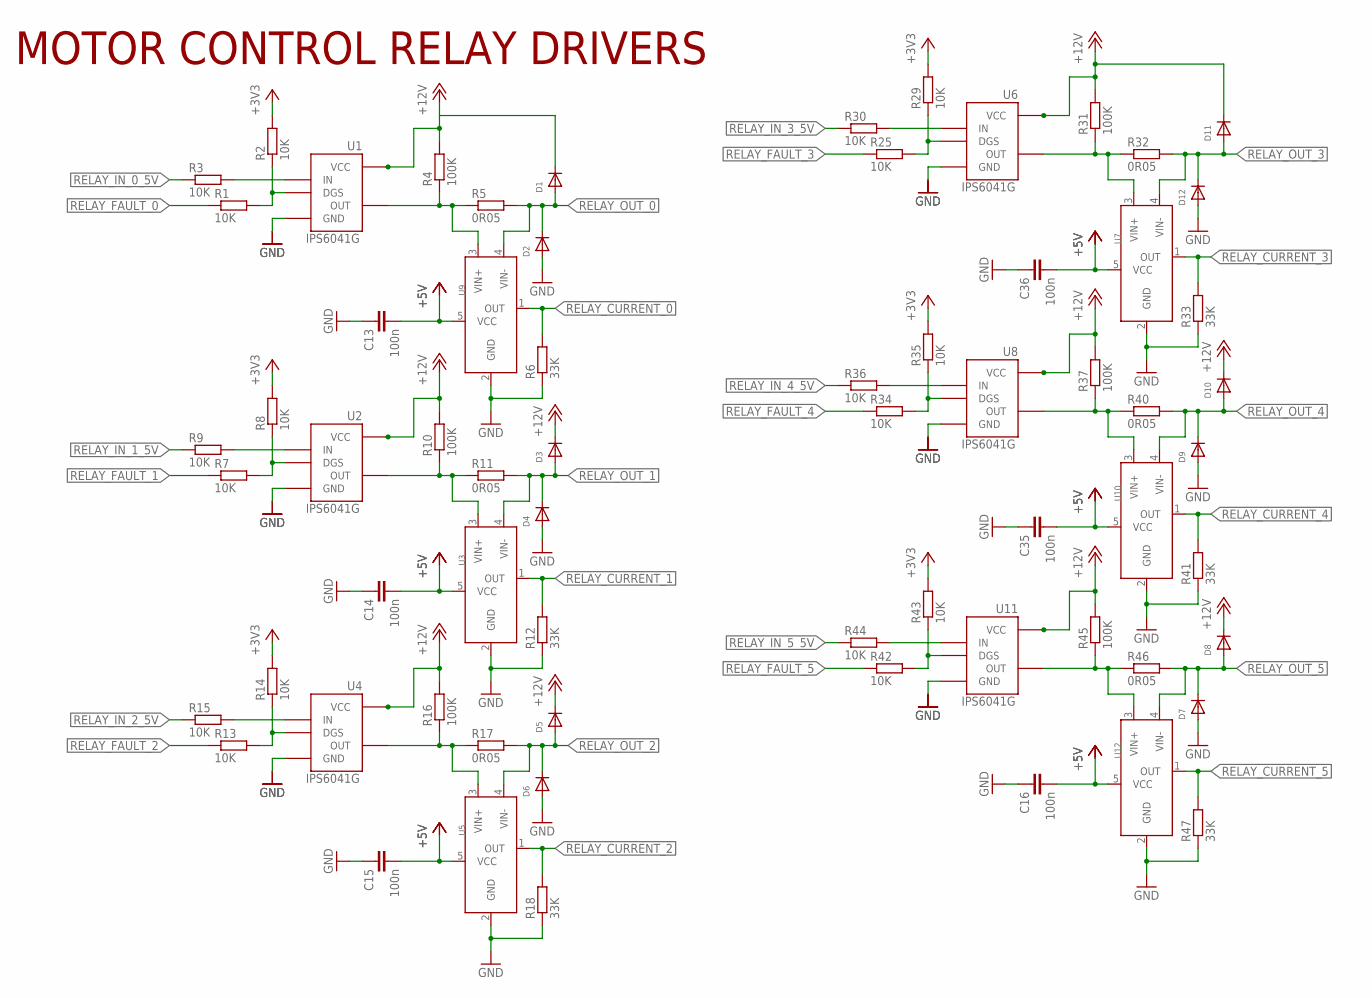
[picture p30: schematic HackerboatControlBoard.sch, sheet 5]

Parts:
C13, C14, C15, C16, C35, C36: 100n; C0603; PARTNO CC0603KRX7R9BB104
D1, D2, D3, D4, D5, D6, D7, D8, D9, D10, D11, D12: DIODESOD-123; SOD-123; PARTNO CDBW140-G
R1, R2, R3, R7, R8, R9, R13, R14, R15, R25, R29, R30, R34, R35, R36, R42, R43, R44: 10K; R0603; PARTNO RNCP0603FTD10K0
R4, R10, R16, R31, R37, R45: 100K; R0603; PARTNO CRCW0603100KFKEA
R5, R11, R17, R32, R40, R46: 0R05; R2512; PARTNO PE2512FKE070R05L
R6, R12, R18, R33, R41, R47: 33K; R0603; PARTNO ERJ-3EKF3302V
U1, U2, U4, U6, U8, U11: IPS6041G; SO08; PARTNO IPS6041GPBF
U3, U5, U7, U9, U10, U12: INA169; SOT23-5L; PARTNO INA169NA/3K

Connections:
+3V3: R2.2, R8.2, R14.2, R29.2, R35.2, R43.2; also elsewhere on the board
+5V: C13.2, C14.2, C15.2, C16.2, C35.2, C36.2, U3.5 (VCC), U5.5 (VCC), U7.5 (VCC), U9.5 (VCC), U10.5 (VCC), U12.5 (VCC); also elsewhere on the board
+12V: D1.C, D3.C, D5.C, D8.C, D10.C, D11.C, R4.2, R10.2, R16.2, R31.2, R37.2, R45.2, U1.5 (VCC), U1.6 (VCC), U1.7 (VCC), U1.8 (VCC), U2.5 (VCC), U2.6 (VCC), U2.7 (VCC), U2.8 (VCC), U4.5 (VCC), U4.6 (VCC), U4.7 (VCC), U4.8 (VCC), U6.5 (VCC), U6.6 (VCC), U6.7 (VCC), U6.8 (VCC), U8.5 (VCC), U8.6 (VCC), U8.7 (VCC), U8.8 (VCC), U11.5 (VCC), U11.6 (VCC), U11.7 (VCC), U11.8 (VCC); also elsewhere on the board
GND: C13.1, C14.1, C15.1, C16.1, C35.1, C36.1, D2.A, D4.A, D6.A, D7.A, D9.A, D12.A, R6.1, R12.1, R18.1, R33.1, R41.1, R47.1, U1.1 (GND), U2.1 (GND), U3.2 (GND), U4.1 (GND), U5.2 (GND), U6.1 (GND), U7.2 (GND), U8.1 (GND), U9.2 (GND), U10.2 (GND), U11.1 (GND), U12.2 (GND); also elsewhere on the board
unnamed: R1.2, R2.1, U1.3 (DGS)
unnamed: R3.2, U1.2 (IN)
unnamed: R4.1, R5.1, U1.4 (OUT), U9.3 (VIN+)
unnamed: R7.2, R8.1, U2.3 (DGS)
unnamed: R9.2, U2.2 (IN)
unnamed: R10.1, R11.1, U2.4 (OUT), U3.3 (VIN+)
unnamed: R13.2, R14.1, U4.3 (DGS)
unnamed: R15.2, U4.2 (IN)
unnamed: R16.1, R17.1, U4.4 (OUT), U5.3 (VIN+)
unnamed: R25.2, R29.1, U6.3 (DGS)
unnamed: R30.2, U6.2 (IN)
unnamed: R31.1, R32.1, U6.4 (OUT), U7.3 (VIN+)
unnamed: R34.2, R35.1, U8.3 (DGS)
unnamed: R36.2, U8.2 (IN)
unnamed: R37.1, R40.1, U8.4 (OUT), U10.3 (VIN+)
unnamed: R42.2, R43.1, U11.3 (DGS)
unnamed: R44.2, U11.2 (IN)
unnamed: R45.1, R46.1, U11.4 (OUT), U12.3 (VIN+)
RELAY_CURRENT_0: R6.2, U9.1 (OUT); also elsewhere on the board
RELAY_CURRENT_1: R12.2, U3.1 (OUT); also elsewhere on the board
RELAY_CURRENT_2: R18.2, U5.1 (OUT); also elsewhere on the board
RELAY_CURRENT_3: R33.2, U7.1 (OUT); also elsewhere on the board
RELAY_CURRENT_4: R41.2, U10.1 (OUT); also elsewhere on the board
RELAY_CURRENT_5: R47.2, U12.1 (OUT); also elsewhere on the board
RELAY_FAULT_0: R1.1; also elsewhere on the board
RELAY_FAULT_1: R7.1; also elsewhere on the board
RELAY_FAULT_2: R13.1; also elsewhere on the board
RELAY_FAULT_3: R25.1; also elsewhere on the board
RELAY_FAULT_4: R34.1; also elsewhere on the board
RELAY_FAULT_5: R42.1; also elsewhere on the board
RELAY_IN_0_5V: R3.1; also elsewhere on the board
RELAY_IN_1_5V: R9.1; also elsewhere on the board
RELAY_IN_2_5V: R15.1; also elsewhere on the board
RELAY_IN_3_5V: R30.1; also elsewhere on the board
RELAY_IN_4_5V: R36.1; also elsewhere on the board
RELAY_IN_5_5V: R44.1; also elsewhere on the board
RELAY_OUT_0: D1.A, D2.C, R5.2, U9.4 (VIN-); also elsewhere on the board
RELAY_OUT_1: D3.A, D4.C, R11.2, U3.4 (VIN-); also elsewhere on the board
RELAY_OUT_2: D5.A, D6.C, R17.2, U5.4 (VIN-); also elsewhere on the board
RELAY_OUT_3: D11.A, D12.C, R32.2, U7.4 (VIN-); also elsewhere on the board
RELAY_OUT_4: D9.C, D10.A, R40.2, U10.4 (VIN-); also elsewhere on the board
RELAY_OUT_5: D7.C, D8.A, R46.2, U12.4 (VIN-); also elsewhere on the board

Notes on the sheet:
MOTOR CONTROL RELAY DRIVERS

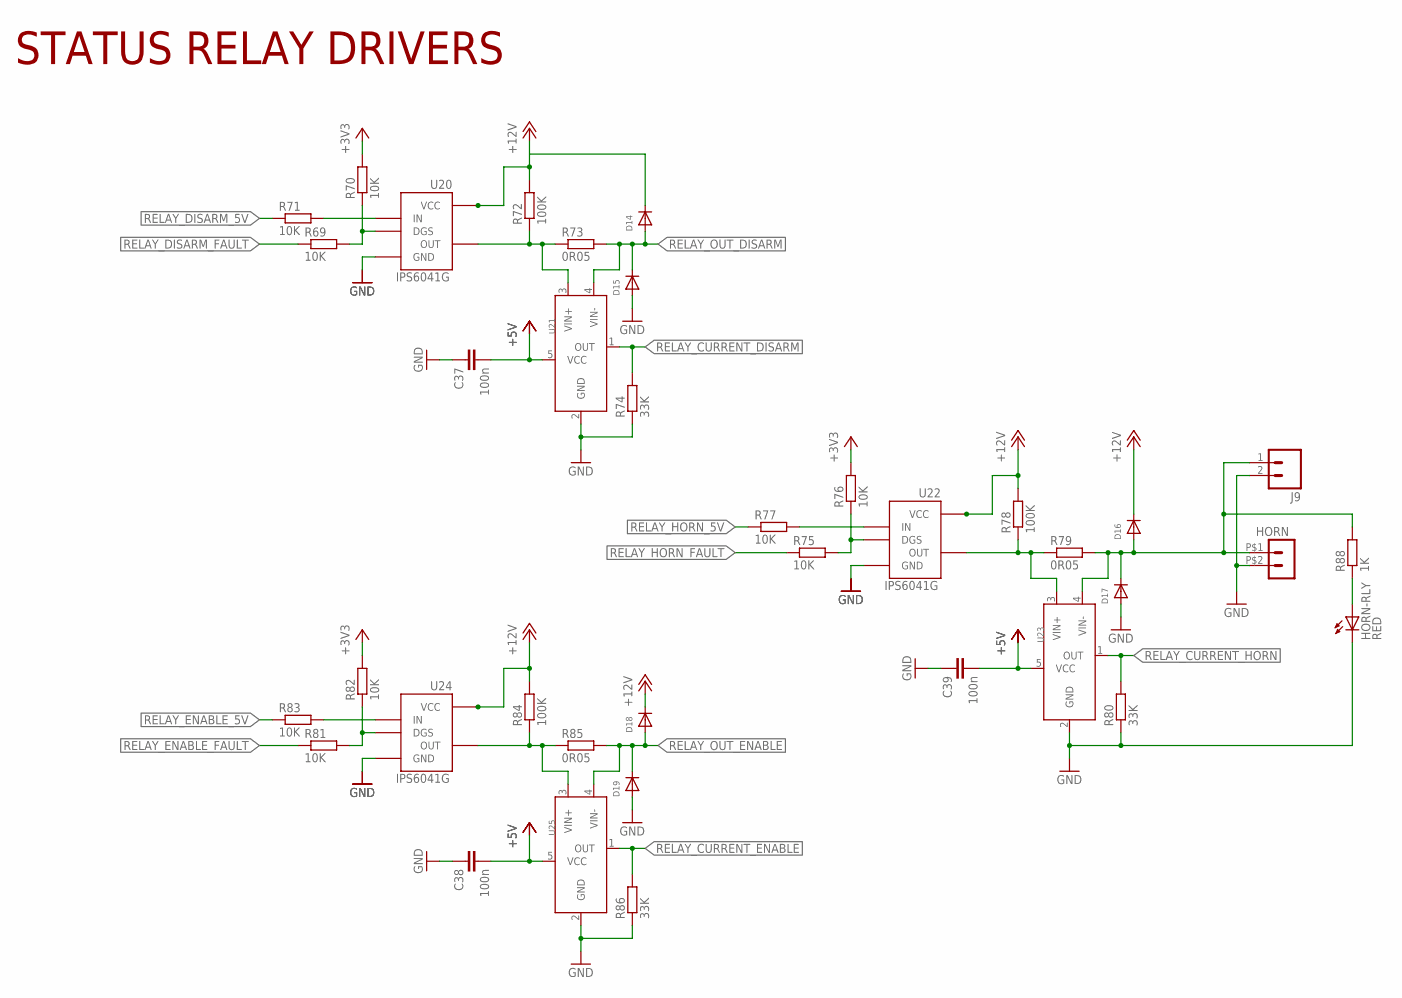
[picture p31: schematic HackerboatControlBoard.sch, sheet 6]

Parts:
C37, C38, C39: 100n; C0603; PARTNO CC0603KRX7R9BB104
D14, D15, D16, D17, D18, D19: DIODESOD-123; SOD-123; PARTNO CDBW140-G
HORN: HEADER_POS2_70555; 70555-POS2; PARTNO 0705550036
HORN-RLY: RED; CHIPLED_0805; PARTNO LH R974-LP-1
J9: M02LOCK; 1X02_LOCK; PARTNO ?
R69, R70, R71, R75, R76, R77, R81, R82, R83: 10K; R0603; PARTNO RNCP0603FTD10K0
R72, R78, R84: 100K; R0603; PARTNO CRCW0603100KFKEA
R73, R79, R85: 0R05; R2512; PARTNO PE2512FKE070R05L
R74, R80, R86: 33K; R0603; PARTNO ERJ-3EKF3302V
R88: 1K; R0603; PARTNO RMCF0603FT1K00
U20, U22, U24: IPS6041G; SO08; PARTNO IPS6041GPBF
U21, U23, U25: INA169; SOT23-5L; PARTNO INA169NA/3K

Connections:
+3V3: R70.2, R76.2, R82.2; also elsewhere on the board
+5V: C37.2, C38.2, C39.2, U21.5 (VCC), U23.5 (VCC), U25.5 (VCC); also elsewhere on the board
+12V: D14.C, D16.C, D18.C, R72.2, R78.2, R84.2, U20.5 (VCC), U20.6 (VCC), U20.7 (VCC), U20.8 (VCC), U22.5 (VCC), U22.6 (VCC), U22.7 (VCC), U22.8 (VCC), U24.5 (VCC), U24.6 (VCC), U24.7 (VCC), U24.8 (VCC); also elsewhere on the board
GND: C37.1, C38.1, C39.1, D15.A, D17.A, D19.A, HORN.P$2 (2), HORN-RLY.C, J9.2, R74.1, R80.1, R86.1, U20.1 (GND), U21.2 (GND), U22.1 (GND), U23.2 (GND), U24.1 (GND), U25.2 (GND); also elsewhere on the board
unnamed: R69.2, R70.1, U20.3 (DGS)
unnamed: R71.2, U20.2 (IN)
unnamed: R72.1, R73.1, U20.4 (OUT), U21.3 (VIN+)
unnamed: R75.2, R76.1, U22.3 (DGS)
unnamed: R77.2, U22.2 (IN)
unnamed: R78.1, R79.1, U22.4 (OUT), U23.3 (VIN+)
unnamed: R81.2, R82.1, U24.3 (DGS)
unnamed: R83.2, U24.2 (IN)
unnamed: R84.1, R85.1, U24.4 (OUT), U25.3 (VIN+)
unnamed: HORN-RLY.A, R88.1
RELAY_CURRENT_DISARM: R74.2, U21.1 (OUT); also elsewhere on the board
RELAY_CURRENT_ENABLE: R86.2, U25.1 (OUT); also elsewhere on the board
RELAY_CURRENT_HORN: R80.2, U23.1 (OUT); also elsewhere on the board
RELAY_DISARM_5V: R71.1; also elsewhere on the board
RELAY_DISARM_FAULT: R69.1; also elsewhere on the board
RELAY_ENABLE_5V: R83.1; also elsewhere on the board
RELAY_ENABLE_FAULT: R81.1; also elsewhere on the board
RELAY_HORN_5V: R77.1; also elsewhere on the board
RELAY_HORN_FAULT: R75.1; also elsewhere on the board
RELAY_OUT_DISARM: D14.A, D15.C, R73.2, U21.4 (VIN-); also elsewhere on the board
RELAY_OUT_ENABLE: D18.A, D19.C, R85.2, U25.4 (VIN-); also elsewhere on the board
RELAY_OUT_HORN: D16.A, D17.C, HORN.P$1 (1), J9.1, R79.2, R88.2, U23.4 (VIN-)

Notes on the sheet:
STATUS RELAY DRIVERS

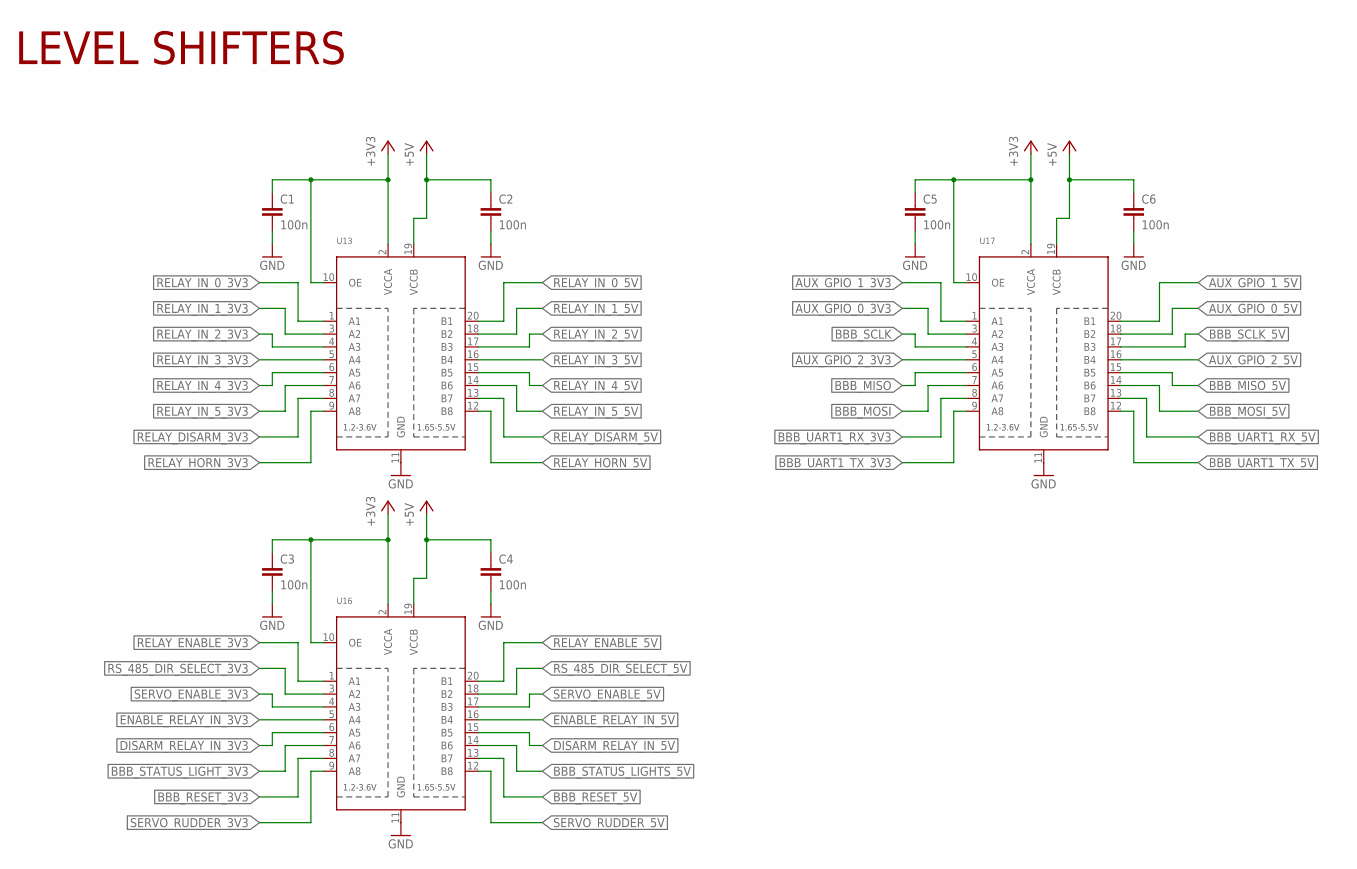
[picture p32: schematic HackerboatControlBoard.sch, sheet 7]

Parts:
C1, C2, C3, C4, C5, C6: 100n; C0603; PARTNO CC0603KRX7R9BB104
U13, U16, U17: TXB0108PWR; TSSOP20; PARTNO TXB0108PWR

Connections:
+3V3: C1.1, C3.1, C5.1, U13.2 (VCCA), U13.10 (OE), U16.2 (VCCA), U16.10 (OE), U17.2 (VCCA), U17.10 (OE); also elsewhere on the board
+5V: C2.1, C4.1, C6.1, U13.19 (VCCB), U16.19 (VCCB), U17.19 (VCCB); also elsewhere on the board
AUX_GPIO_0_3V3: U17.3 (A2); also elsewhere on the board
AUX_GPIO_0_5V: U17.18 (B2); also elsewhere on the board
AUX_GPIO_1_3V3: U17.1 (A1); also elsewhere on the board
AUX_GPIO_1_5V: U17.20 (B1); also elsewhere on the board
AUX_GPIO_2_3V3: U17.5 (A4); also elsewhere on the board
AUX_GPIO_2_5V: U17.16 (B4); also elsewhere on the board
BBB_MISO: U17.6 (A5); also elsewhere on the board
BBB_MISO_5V: U17.15 (B5); also elsewhere on the board
BBB_MOSI: U17.7 (A6); also elsewhere on the board
BBB_MOSI_5V: U17.14 (B6); also elsewhere on the board
BBB_RESET_3V3: U16.8 (A7); also elsewhere on the board
BBB_RESET_5V: U16.13 (B7); also elsewhere on the board
BBB_SCLK: U17.4 (A3); also elsewhere on the board
BBB_SCLK_5V: U17.17 (B3); also elsewhere on the board
BBB_STATUS_LIGHTS_5V: U16.14 (B6); also elsewhere on the board
BBB_STATUS_LIGHT_3V3: U16.7 (A6)
BBB_UART1_RX_3V3: U17.8 (A7); also elsewhere on the board
BBB_UART1_RX_5V: U17.13 (B7); also elsewhere on the board
BBB_UART1_TX_3V3: U17.9 (A8); also elsewhere on the board
BBB_UART1_TX_5V: U17.12 (B8); also elsewhere on the board
DISARM_RELAY_IN_3V3: U16.6 (A5); also elsewhere on the board
DISARM_RELAY_IN_5V: U16.15 (B5); also elsewhere on the board
ENABLE_RELAY_IN_3V3: U16.5 (A4); also elsewhere on the board
ENABLE_RELAY_IN_5V: U16.16 (B4); also elsewhere on the board
GND: C1.2, C2.2, C3.2, C4.2, C5.2, C6.2, U13.11 (GND), U16.11 (GND), U17.11 (GND); also elsewhere on the board
RELAY_DISARM_3V3: U13.8 (A7); also elsewhere on the board
RELAY_DISARM_5V: U13.13 (B7); also elsewhere on the board
RELAY_ENABLE_3V3: U16.1 (A1); also elsewhere on the board
RELAY_ENABLE_5V: U16.20 (B1); also elsewhere on the board
RELAY_HORN_3V3: U13.9 (A8); also elsewhere on the board
RELAY_HORN_5V: U13.12 (B8); also elsewhere on the board
RELAY_IN_0_3V3: U13.1 (A1); also elsewhere on the board
RELAY_IN_0_5V: U13.20 (B1); also elsewhere on the board
RELAY_IN_1_3V3: U13.3 (A2); also elsewhere on the board
RELAY_IN_1_5V: U13.18 (B2); also elsewhere on the board
RELAY_IN_2_3V3: U13.4 (A3); also elsewhere on the board
RELAY_IN_2_5V: U13.17 (B3); also elsewhere on the board
RELAY_IN_3_3V3: U13.5 (A4); also elsewhere on the board
RELAY_IN_3_5V: U13.16 (B4); also elsewhere on the board
RELAY_IN_4_3V3: U13.6 (A5); also elsewhere on the board
RELAY_IN_4_5V: U13.15 (B5); also elsewhere on the board
RELAY_IN_5_3V3: U13.7 (A6); also elsewhere on the board
RELAY_IN_5_5V: U13.14 (B6); also elsewhere on the board
RS_485_DIR_SELECT_3V3: U16.3 (A2); also elsewhere on the board
RS_485_DIR_SELECT_5V: U16.18 (B2); also elsewhere on the board
SERVO_ENABLE_3V3: U16.4 (A3); also elsewhere on the board
SERVO_ENABLE_5V: U16.17 (B3); also elsewhere on the board
SERVO_RUDDER_3V3: U16.9 (A8); also elsewhere on the board
SERVO_RUDDER_5V: U16.12 (B8); also elsewhere on the board

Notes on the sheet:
LEVEL SHIFTERS


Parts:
ACC_POWER: PINHD-2X8_2.54; 2X08; PARTNO *
BBB_RESET: HEADER_POS3_70555; 70555-POS3; PARTNO 0705550037
C47: 100n; C0603; PARTNO CC0603KRX7R9BB104
D24, D25, D26, D28: 5V; SOD-123; PARTNO SMF5.0A
FAULT_0, FAULT_1, FAULT_2, FAULT_3, FAULT_4, FAULT_5: RED; CHIPLED_0805; PARTNO LH R974-LP-1
FAULT_DISARM: RED; CHIPLED_0805; PARTNO LH R974-LP-1
FAULT_ENABLE: RED; CHIPLED_0805; PARTNO LH R974-LP-1
FAULT_HORN: RED; CHIPLED_0805; PARTNO LH R974-LP-1
IC3: 74AHC1G04DBV; SOT23-5; PARTNO MC74HC1G04DTT1G
J1, J10: M03LOCK; 1X03_LOCK; PARTNO ?
J3: M04LOCK; 1X04_LOCK; PARTNO *
POE-DEVICE: RJ45; RJ45-8; PARTNO 615008137121
POE-LAN: RJ45; RJ45-8; PARTNO 615008137121
POWER_MON: PINHD-2X6_2.54; 2X06; PARTNO *
R92, R93, R94, R96, R101, R102, R103, R104, R105, R106, R107, R108, R109: 1K; R0603; PARTNO RMCF0603FT1K00
SERIAL_CONSOLE: HEADER_POS4_70555; 70555-POS4; PARTNO 0705550038
STEERING: HEADER_POS3_70555; 70555-POS3; PARTNO 0705550037

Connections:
+3V3: ACC_POWER.7, ACC_POWER.8, ACC_POWER.9, ACC_POWER.10; also elsewhere on the board
+5V: ACC_POWER.1, ACC_POWER.2, ACC_POWER.3, ACC_POWER.4, BBB_RESET.P$1 (1), C47.1, IC3.5 (VCC), J10.1, POWER_MON.1, POWER_MON.5, POWER_MON.9, R101.2, R102.2, R103.2, R104.2, R105.2, R106.2, R107.2, R108.2, R109.2; also elsewhere on the board
+7V4: ACC_POWER.15, ACC_POWER.16, J1.1, STEERING.P$1 (1); also elsewhere on the board
+15V: ACC_POWER.13, ACC_POWER.14, POE-DEVICE.4, POE-DEVICE.5; also elsewhere on the board
AUX_ADC_0: POWER_MON.10; also elsewhere on the board
AUX_ADC_1: POWER_MON.11; also elsewhere on the board
BBB_RESET_5V: IC3.4 (O); also elsewhere on the board
BBB_UART0_RX: D26.C, R93.2; also elsewhere on the board
BBB_UART0_TX: D25.C, R94.2; also elsewhere on the board
CHARGE_CURRENT: POWER_MON.7; also elsewhere on the board
CHARGE_VOLTAGE: POWER_MON.6; also elsewhere on the board
GND: ACC_POWER.5, ACC_POWER.6, ACC_POWER.11, ACC_POWER.12, BBB_RESET.P$3 (3), C47.2, D24.A, D25.A, D26.A, D28.A, IC3.3 (GND), J1.3, J3.4, J10.3, POE-DEVICE.7, POE-DEVICE.8, POWER_MON.4, POWER_MON.8, POWER_MON.12, SERIAL_CONSOLE.P$4 (4), STEERING.P$3 (3); also elsewhere on the board
MOT_CURRENT: POWER_MON.3; also elsewhere on the board
MOT_VOLTAGE: POWER_MON.2; also elsewhere on the board
unnamed: D28.C, IC3.2 (I), R96.2
unnamed: POE-DEVICE.1, POE-LAN.1
unnamed: POE-DEVICE.2, POE-LAN.2
unnamed: POE-DEVICE.3, POE-LAN.3
unnamed: POE-DEVICE.6, POE-LAN.6
unnamed: J1.2, R92.1, STEERING.P$2 (2)
unnamed: J3.2, R93.1, SERIAL_CONSOLE.P$2 (2)
unnamed: J3.3, R94.1, SERIAL_CONSOLE.P$3 (3)
unnamed: BBB_RESET.P$2 (2), J10.2, R96.1
unnamed: FAULT_0.A, R101.1
unnamed: FAULT_1.A, R102.1
unnamed: FAULT_2.A, R103.1
unnamed: FAULT_3.A, R104.1
unnamed: FAULT_4.A, R105.1
unnamed: FAULT_5.A, R106.1
unnamed: FAULT_ENABLE.A, R107.1
unnamed: FAULT_DISARM.A, R108.1
unnamed: FAULT_HORN.A, R109.1
RELAY_DISARM_FAULT: FAULT_DISARM.C; also elsewhere on the board
RELAY_ENABLE_FAULT: FAULT_ENABLE.C; also elsewhere on the board
RELAY_FAULT_0: FAULT_0.C; also elsewhere on the board
RELAY_FAULT_1: FAULT_1.C; also elsewhere on the board
RELAY_FAULT_2: FAULT_2.C; also elsewhere on the board
RELAY_FAULT_3: FAULT_3.C; also elsewhere on the board
RELAY_FAULT_4: FAULT_4.C; also elsewhere on the board
RELAY_FAULT_5: FAULT_5.C; also elsewhere on the board
RELAY_HORN_FAULT: FAULT_HORN.C; also elsewhere on the board
SERVO_RUDDER_5V: D24.C, R92.2; also elsewhere on the board

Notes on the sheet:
EXTERNAL CONNECTORS
FAULT LIGHTS

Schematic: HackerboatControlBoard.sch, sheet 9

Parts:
C19: 10u; C1210; PARTNO UMK325BJ106MM
C20: 22u; C1210; PARTNO GRM32ER61E226KE15K
CELL: FONA; FONA-3G; PARTNO BCS-118-L-S-TE
D27: 5V; SOD-123; PARTNO SMF5.0A
F2: PTC-2920; 2920L; PARTNO MF-LSMF300/24X-2
GPS: ULTIMATE-GPS; PARTNO BCS-109-L-S-TE
IC5: V7805-2000; TO220V; PARTNO V7805-2000
IMU: 9-DOF-BREAKOUT; PARTNO BCS-110-L-S-TE
J2: M03LOCK; 1X03_LOCK; PARTNO ?
J5: M09LOCK; 1X09_LOCK; PARTNO *
J6: M10LOCK; 1X10_LOCK; PARTNO *
J7: M18_; 1X18; PARTNO *
R19: 4K7'; R0603; PARTNO RC1608J472CS
R20: 4K7; R0603; PARTNO RC1608J472CS
R95: 1K; R0603; PARTNO RMCF0603FT1K00
STATUS_LIGHTS: HEADER_POS3_70555; 70555-POS3; PARTNO 0705550037

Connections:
+3V3: CELL.VIO (15), J7.15, R19.2, R20.2; also elsewhere on the board
+5V: CELL.5V (18), GPS.VIN (5), IMU.VIN (1), J5.2, J6.1, J7.18; also elsewhere on the board
+12V: C19.1, IC5.1 (VI); also elsewhere on the board
BBB_I2C_1_SCL: IMU.SCL (4), J6.4, R19.1; also elsewhere on the board
BBB_I2C_1_SDA: IMU.SDA (5), J6.5, R20.1; also elsewhere on the board
BBB_STATUS_LIGHTS_5V: D27.C, R95.2; also elsewhere on the board
CELL_CTS: CELL.CTS (9), J7.9; also elsewhere on the board
CELL_KEY: CELL.KEY (8), J7.8; also elsewhere on the board
CELL_NET_STATUS: CELL.NS (5), J7.5; also elsewhere on the board
CELL_POWER_STATUS: CELL.PS (6), J7.6; also elsewhere on the board
CELL_RESET: CELL.RST (14), J7.14; also elsewhere on the board
CELL_RING: CELL.RI (7), J7.7; also elsewhere on the board
CELL_RTS: CELL.RTS (11), J7.11; also elsewhere on the board
CELL_RX: CELL.RX (13), J7.13; also elsewhere on the board
CELL_TX: CELL.TX (12), J7.12; also elsewhere on the board
GND: C19.2, C20.2, CELL.GND (16), D27.A, GPS.GND (6), IC5.2 (GND), IMU.GND (3), J2.3, J5.3, J6.3, J7.16, STATUS_LIGHTS.P$3 (3); also elsewhere on the board
GNSS_ENABLE: GPS.EN (8), J5.8; also elsewhere on the board
GNSS_FIX: GPS.FIX (7), J5.6; also elsewhere on the board
GNSS_RX: GPS.RX (2), J5.4; also elsewhere on the board
GNSS_TX: GPS.TX (3), J5.5; also elsewhere on the board
unnamed: GPS.PPS (1), J5.1
unnamed: GPS.VBAT (4), J5.7
unnamed: IMU.3VO (2), J6.2
unnamed: IMU.GINT (6), J6.6
unnamed: IMU.GRDY (7), J6.7
unnamed: IMU.LIN1 (8), J6.8
unnamed: IMU.LIN2 (9), J6.9
unnamed: IMU.LRDY (10), J6.10
unnamed: GPS.3V3 (9), J5.9
unnamed: CELL.SPKR+ (2), J7.2
unnamed: CELL.MIC- (3), J7.3
unnamed: CELL.MIC+ (4), J7.4
unnamed: CELL.DTR (10), J7.10
unnamed: CELL.BAT (17), J7.17
unnamed: CELL.SPKR- (1), J7.1
unnamed: F2.P$1 (1), J2.1, STATUS_LIGHTS.P$1 (1)
unnamed: C20.1, F2.P$2 (2), IC5.3 (VO)
unnamed: J2.2, R95.1, STATUS_LIGHTS.P$2 (2)



Board: 2 copper layers, 114.3 x 195.6 mm, 287 parts (18 on the bottom side), 256 nets.

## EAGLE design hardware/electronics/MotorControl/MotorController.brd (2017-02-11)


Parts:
C1, C2: C-EUC0603; C0603
C3, C4: C-EUC1206; C1206
H1, H2, H3, H4: MOUNT-PAD-ROUND3.2; 3,2-PAD
J1: AVR_SPI_PRG_6PTH; 2X3
U1: ARDUINOR3-BPLACE
U2: ATMEGA328P_TQFP; TQFP32-08
U3: V_REG_317SMD; SOT223
U$1: RS485SOIC; SO08
X1: HEADER_POS3_70555; 70555-POS3

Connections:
3V: U1.3V
+5V: C1.1, C2.2, C3.2, J1.2, U1.5V, U2.4 (VCC), U2.6 (VCC), U2.18 (AVCC), U3.2 (OUT), U$1.8 (VCC)
GND: C1.2, C2.1, C3.1, C4.1, J1.6, U1.GND, U1.GND1, U1.GND2, U2.3 (GND), U2.5 (GND), U2.21 (AGND), U3.1 (ADJ), U$1.5 (GND), X1.P$3 (3)
M1EN-DIAG: U1.D6, U2.19 (ADC6)
M1INA: U1.D2, U2.25 (PC2(ADC2))
M1INB: U1.D4, U2.26 (PC3(ADC3))
M1PWM: U1.D9, U2.13 (PB1(OC1A))
M2EN-DIAG: U1.D12, U2.22 (ADC7)
M2INA: U1.D7, U2.27 (PC4(ADC4/SDA))
M2INB: U1.D8, U2.28 (PC5(ADC5/SCL))
M2PWM: U1.D10, U2.14 (PB2(SS/OC1B))
unnamed: J1.5, U2.29 (PC6(/RESET))
unnamed: J1.3, U2.17 (PB5(SCK))
unnamed: J1.1, U2.16 (PB4(MISO))
unnamed: J1.4, U2.15 (PB3(MOSI/OC2))
unnamed: U2.32 (PD2(INT0)), U$1.2 (/RE), U$1.3 (DE)
unnamed: U2.30 (PD0(RXD)), U$1.1 (RO)
unnamed: U2.31 (PD1(TXD)), U$1.4 (DI)
unnamed: U1.A0, U2.23 (PC0(ADC0))
unnamed: U1.A1, U2.24 (PC1(ADC1))
unnamed: U$1.7 (B), X1.P$1 (1)
unnamed: U$1.6 (A), X1.P$2 (2)
VIN: C4.2, U1.VIN, U3.3 (IN)


Board: 2 copper layers, 58.4 x 53.3 mm, 14 parts (0 on the bottom side), 22 nets.

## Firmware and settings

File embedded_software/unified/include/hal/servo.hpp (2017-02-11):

/******************************************************************************
 * Hackerboat Beaglebone Servo module
 * hal/servo.hpp
 * This module manipulates the servo output
 * see the Hackerboat documentation for more details
 * Code is derived, in a general sense, from the Arduino Servo library
 * Written by Pierce Nichols, Aug 2016
 * 
 * Version 0.1: First alpha
 *
 ******************************************************************************/
 
#ifndef SERVO_H
#define SERVO_H
 
#include "config.h"
#include <math.h>
#include <string>
#include <inttypes.h>

#define MIN_PULSE_WIDTH			1000	// the shortest pulse sent to a servo, microseconds  
#define MAX_PULSE_WIDTH      	2000	// the longest pulse sent to a servo, microseconds 
#define DEFAULT_PULSE_WIDTH  	1500	// default pulse width when servo is attached
#define DEFAULT_FREQUENCY    	100		// servo frequency, Hz

class Servo {
	public:
		Servo();
		bool attach(int port, 							/**< Attach servo to named pin on the named port {8|9}. Returns true if successful. */
					int pin,
					long min = MIN_PULSE_WIDTH,
					long max = MAX_PULSE_WIDTH,
					long freq = DEFAULT_FREQUENCY);		
		void detach();									/**< Detach servo from the pin */
		bool write(double value);						/**< Set the servo position, from -100.0 to +100.0. Returns true if successful, false is unsuccessful or out of range. */
		bool writeMicroseconds(unsigned long value);	/**< Set the servo position in microseconds. Returns true if successful, false is unsuccessful or out of range. */
		bool setFrequency(unsigned long freq);			/**< Set servo frequency in Hz. Returns true if successful. */
		bool setMax (unsigned long max);				/**< Set the maximum servo value, in microseconds. Returns false if max time period is longer than one time period at the current frequency */
		bool setMin (unsigned long min);				/**< Set the minimum servo value, in microseconds. Returns false is larger than max */
		long getMax () {return _max/1000.0;};
		long getMin () {return _min/1000.0;};
		double read();									/**< Read the current servo value. */
		unsigned long readMicroseconds();				/**< Read the current servo value, in microseconds. */
		bool isAttached() {return attached;};			/**< Check if this object is attached to a pin. */	
	private:
		std::string getServoPath (int port, int pin);
		bool writeMicroseconds();						/**< Set pwm channel to the currently stored frequency */
		bool setFrequency();							/**< Set pwm channel to the currently stored frequency */

		std::string path = "";
		std::string pinname = "";
		int majornum = -1;
		int minornum = -1;
		// all time values in nanoseconds
		unsigned long _min = 1000000;
		unsigned long _max = 2000000;
		unsigned long _freq = 20000000;
		unsigned long _center = 1500000;
		unsigned long _val = 1500000;
		bool attached = false;
	
};

#endif 

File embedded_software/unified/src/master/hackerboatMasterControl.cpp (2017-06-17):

/******************************************************************************
 * Hackerboat Beaglebone Master Control program
 * hackerboatMasterControl.cpp
 * This program is the core vessel control program
 * see the Hackerboat documentation for more details
 *
 * Written by Pierce Nichols, Aug 2016
 *
 * Version 0.1: First alpha
 *
 ******************************************************************************/

#include "hal/config.h"
#include <stdlib.h>
#include <stdio.h>
#include <string>
#include <chrono>
#include <fstream>
#include "boatState.hpp"
#include "boatModes.hpp"
#include "autoModes.hpp"
#include "rcModes.hpp"
#include "navModes.hpp"
#include "stateMachine.hpp"
#include "location.hpp"
#include "orientation.hpp"
#include "pid.hpp"
#include "aio-rest.hpp"
#include "rapidjson/rapidjson.h"
#include "hal/adcInput.hpp"
#include "hal/gpsdInput.hpp"
#include "hal/orientationInput.hpp"
#include "hal/RCinput.hpp"
#include "hal/servo.hpp"
#include "hal/throttle.hpp"
#include "waypoint.hpp"
#include "easylogging++.h"
#include "configuration.hpp"

#include "util.hpp"

#define ELPP_STL_LOGGING

INITIALIZE_EASYLOGGINGPP

//void inputBB (BoatState &state, long stepNum);
//void outputBB (BoatState &state, long stepNum);

int main (int argc, char **argv) {
	cerr << "Starting up..." << std::endl;
	bool declinationLoaded = false;

    // Load configuration from file
    el::Configurations conf("/home/debian/hackerboat/embedded_software/unified/setup/log.conf");
    // Actually reconfigure all loggers instead
    el::Loggers::reconfigureAllLoggers(conf);
	START_EASYLOGGINGPP(argc, argv);
	Args::getargs()->load(argc, argv);
	Conf::get()->load();

	// system setup
	BoatState state;
	state.rc = new RCInput();
	state.adc = new ADCInput();
	state.health = new HealthMonitor(state.adc);
	state.gps = new GPSdInput();
	state.relays = RelayMap::instance();
	state.rudder = new Servo();
	state.throttle = new Throttle();
	state.orient = new OrientationInput(SensorOrientation::SENSOR_AXIS_Z_UP);

	// start the input threads
	if (!state.rudder->attach(Conf::get()->rudderPort(), Conf::get()->rudderPin())) {
		LOG(FATAL) << "Rudder failed to attach";
		return -1;
	}
	if (!state.orient->begin()) {
		LOG(FATAL)  << "Orientation subsystem failed to start";
		return -1;
	}
	if (!state.rc->begin()) {
		LOG(FATAL)  << "RC subsystem failed to start";
		return -1;
	}
	if (!state.gps->begin()) {
		LOG(FATAL)  << "GPS subsystem failed to start";
		return -1;
	}
	if (!state.adc->begin()) {
		LOG(FATAL)  << "ADC subsystem failed to start";
		return -1;
	}
	state.relays->init();
	
	// AIO REST setup
	AIO_Rest myrest(&state);
	cerr << "Creating publishing map..." << endl;
	PubFuncMap *mypubmap = new PubFuncMap {	{"SpeedLocation", new pub_SpeedLocation(&state, &myrest)},
											{"Mode", new pub_Mode(&state, &myrest)},
											{"MagneticHeading", new pub_MagHeading(&state, &myrest)},
											{"GPSCourse", new pub_GPSCourse(&state, &myrest)},
											{"BatteryVoltage", new pub_BatteryVoltage(&state, &myrest)},
											{"RudderPosition", new pub_RudderPosition(&state, &myrest)},
											{"ThrottlePosition", new pub_ThrottlePosition(&state, &myrest)},
											{"FaultString", new pub_FaultString(&state, &myrest)},
											{"Waypoint", new pub_Waypoint(&state, &myrest)} };
	cerr << "Publishing map created..." << endl;
	SubFuncMap *mysubmap = new SubFuncMap {{"Command", new sub_Command(&state, &myrest)}};
	cerr << "Subscription map created..." << endl;
	myrest.setPubFuncMap(mypubmap);
	myrest.setSubFuncMap(mysubmap);
	myrest.begin();

	// create the boat mode
	BoatModeBase *mode, *oldmode = {0};
	mode = BoatModeBase::factory(state, BoatModeEnum::START);

	// load KML file
	if (!state.waypointList.loadKML("/home/debian/hackerboat/embedded_software/unified/test_data/waypoint/2017Mar25.kml")) {
		LOG(ERROR)  << "Waypoint list failed to load";
		cerr << "KML failed to load" << endl;
		//return -1;
	}

	cerr << "All configured -- entering state" << std::endl;
	LOG(INFO) << "CSV," << state.getCSVheaders();

	// run the boat
	for (;;) {
		// kick the dog
		ofstream wdfile;
		wdfile.open(Conf::get()->wdFile());
		wdfile << "1" << endl;
		wdfile.close();

		// read inputs
		state.lastFix.copy(state.gps->getFix());
		state.health->readHealth();

		// check if we have a valid fix and have not loaded the declination -- if so, load it. 
		if (state.lastFix.isValid() && !declinationLoaded) {
			declinationLoaded = state.orient->getOrientation()->updateDeclination(state.lastFix.fix);
		}

		// run the state
		auto endtime = std::chrono::system_clock::now() + 100ms;
		if (state.commandCnt()) {
			cerr << to_string(state.commandCnt()) << " commands in the queue" << endl;
			cerr << to_string(state.executeCmds(0)) << " commands successfully executed" << endl;
		}
		oldmode = mode;
		mode = mode->execute();
		if (mode != oldmode) REMOVE(oldmode);		
		LOG_EVERY_N(5, INFO) << "CSV," << state.getCSV();
		std::this_thread::sleep_until(endtime);
	}

	return 0;

}

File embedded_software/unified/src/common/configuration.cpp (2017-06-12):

/******************************************************************************
 * Hackerboat Beaglebone configuration
 * configuration.hpp
 * This is a library for loading the configuration from a json file
 * see the Hackerboat documentation for more details
 *
 * Written by Pierce Nichols, Apr 2017
 *
 * Version 0.1: First alpha
 *
 ******************************************************************************/

#include "configuration.hpp"
#include <string>
#include <chrono>
#include <iostream>
#include <cstdio>
#include <tuple>
#include <vector>
#include "util.hpp"
#include "rapidjson/rapidjson.h"
#include "rapidjson/document.h"
#include "rapidjson/pointer.h"
#include "rapidjson/filereadstream.h"
#include "private-config.h"

using namespace std;

int Conf::Fetch(const string& name, string& target) {
	if (d.HasMember(name.c_str()) && d[name.c_str()].IsString()) {
		target = d[name.c_str()].GetString();
		return 1;
	}
	return 0;
}

int Conf::Fetch(const string& name, unsigned int& target) {
	if (d.HasMember(name.c_str()) && d[name.c_str()].IsUint()) {
		target = d[name.c_str()].GetUint();
		return 1;
	}
	return 0;
}

int Conf::Fetch(const string& name, uint8_t& target) {
	if (d.HasMember(name.c_str()) && d[name.c_str()].IsUint()) {
		unsigned int tmp = d[name.c_str()].GetUint();
		if (tmp > 255) return 0;
		target = tmp;
		return 1;
	}
	return 0;
}

int Conf::Fetch(const string& name, float& target) {
	if (d.HasMember(name.c_str()) && d[name.c_str()].IsFloat()) {
		target = d[name.c_str()].GetFloat();
		return 1;
	}
	return 0;
}

int Conf::Fetch(const string& name, int& target) {
	if (d.HasMember(name.c_str()) && d[name.c_str()].IsInt()) {
		target = d[name.c_str()].GetInt();
		return 1;
	}
	return 0;
}

int Conf::Fetch(const string& name, sysdur& duration) {
	if (d.HasMember(name.c_str()) && d[name.c_str()].IsString()) {
		if (parseDuration(d[name.c_str()].GetString(), duration)) return 1;
	}
	return 0;
}

int Conf::Fetch(const string& name, Value& v) {
	if (d.HasMember(name.c_str()) && d[name.c_str()].IsObject()) {
		v = d[name.c_str()].GetObject();
		return 1;
	}
	return 0;
}

Conf::Conf () {
	_gpsdAddress 		= "127.0.0.1";
	_gpsdPort			= (3001);
	_adcUpperAddress	= (0x1f);
	_adcLowerAddress	= (0x1d);
	_adcI2Cbus			= (2);
	_imuI2Cbus			= (1);
	_throttleMax	 	= (5);
	_throttleMin	 	= (-5);
	_rudderMax			= (100);
	_rudderMin			= (-100);
	_rudderDir			= (1);
	_rudderPeriod		= (100);
	_courseMax			= (360.0);
	_courseMin			= (0.0);
	_lightCount			= (72);
	_aisMaxTime			= (600s);
	_configPinPath		= "/usr/local/bin/config-pin";
	_disarmInputPort	= (8);
	_disarmInputPin		= (22);
	_armInputPort 		= (8);
	_armInputPin 		= (20);
	_servoEnbPort 		= (8);
	_servoEnbPin 		= (19);
	_rudderPort 		= (9);
	_rudderPin			= (16);
	_pidKp				= (10.0);
	_pidKi 				= (0.1);
	_pidKd				= (0.0);
	_gpsBufSize			= (2000);
	_gpsAvgLen			= (10);
	_imuMagOffset		= {330, -86, 386};
	_imuMagScale		= {0.15835, 0.18519, 0.18149};
	_RCchannelMap 		= {	{"throttle", (0)},
							{"rudder", (3)},
							{"auto", (4)},
							{"mode", (5)},
							{"courseSelect", (6)},
							{"horn", (7)},
							{"channelCount", (18)} };
	_RClimits			= {	{"min", (171)},
							{"max", (1811)},
							{"middlePosn", (991)},
							{"middleTol", (200)} }; 						
	_RCserialPath		= "/dev/ttyS5";
	_autoDefaultThrottle = (5);
	_autoWaypointTol	= (50.0);
	_anchorDeadband		= (5.0);
	_anchorThrottleGain	= (1.0);
	_hornTime 			= (2s);
	_disarmPulseLen		= (50ms);
	_armPulseLen		= (50ms);
	_imuReadPeriod		= (10ms);
	_adcReadPeriod		= (10ms);
	_rcReadPeriod		= (8ms);
	_gpsReadPeriod		= (20ms);
	_startBatMinVolt	= (12.0);
	_lowBatCutoffVolt 	= (10.0);
	_adcUpperChanList	= {"RED", "DIR", "YLWWHT", "REDWHT", "YLW", "WHT", "DISARM", "ENABLE"};
	_adcLowerChanList	= {"HORN", "mot_i", "mot_v", "charge_v", "charge_i", "aux_0", "aux_1", "servo_i"};
	_adcExternRefVolt	= (5.0);
	_batmonPath			= "/sys/devices/platform/ocp/44e0d000.tscadc/TI-am335x-adc/iio:device0/in_voltage1_raw";
	_batmonName			= "battery_mon";
	_restConf			= {	{"key_header", "X-AIO-Key:"},
							{"host", "https://io.adafruit.com/api/v2/"},
							{"username", restUsername},
							{"key", restKey},
							{"group", ""},
							{"datatype", "json"} };
	_restPubPeriod		= (1000ms);
	_restSubPeriod		= (200ms);
	_restDelay			= (1ms);
	_restTimeout		= (200ms);
	_restMaxBuf			= (50000);
	_restMaxCount		= (5000);
	_wdFile				= "/tmp/watchdog";
	_wdTimeout			= (30s);
	_relayInit			= { { "RED", { "RED", 8, 3, 8, 4 } },
							{ "DIR", { "DIR", 8, 5, 8, 6 } }, 
							{ "YLWWHT", { "YLWWHT", 8, 7, 8, 8 } }, 
							{ "REDWHT", { "REDWHT", 8, 9, 8, 10 } }, 
							{ "YLW", { "YLW", 8, 11, 8, 12 } }, 
							{ "WHT", { "WHT", 8, 13, 8, 14 } }, 
							{ "DISARM", { "DISARM", 8, 15, 8, 16 } }, 
							{ "HORN", { "HORN", 8, 17, 8, 18 } }, 
							{ "ENABLE", { "ENABLE", 8, 24, 8, 26 } } };
	_RCchannelCount		= (18);
	_aisMaxDistance		= (10000);
	_selfTestDelay		= (30s);
}
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

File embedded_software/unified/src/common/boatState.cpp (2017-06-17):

/******************************************************************************
 * Hackerboat Beaglebone boat state module
 * boatState.cpp
 * see the Hackerboat documentation for more details
 * Written by Pierce Nichols, Sep 2016
 *
 * Version 0.1: First alpha
 *
 ******************************************************************************/

#include <chrono>
#include <string>
#include <stdlib.h>
#include <stdio.h>
#include <list>
#include "hackerboatRoot.hpp"
#include "enumtable.hpp"
#include "location.hpp"
#include "gps.hpp"
#include "hal/config.h"
#include "enumdefs.hpp"
#include "healthMonitor.hpp"
#include "waypoint.hpp"
#include "dodge.hpp"
#include "hal/relay.hpp"
#include "hal/gpio.hpp"
#include "hal/adcInput.hpp"
#include "hal/RCinput.hpp"
#include "hal/gpsdInput.hpp"
#include "boatState.hpp"
#include "easylogging++.h"
#include "util.hpp"

using namespace std;
using namespace rapidjson;

#define MAKE_FUNC(func) { #func, std::function<bool(Value&, BoatState*)>( Command::func ) }

BoatState::BoatState () {
	VLOG(2) << "Creating new BoatState object";
	relays = RelayMap::instance();
	rudder = new Servo();
	rudder->attach(Conf::get()->rudderPort(), Conf::get()->rudderPin());
	if (!disarmInput.isInit()) {
		disarmInput.setPort(Conf::get()->disarmInputPort());
		disarmInput.setPin(Conf::get()->disarmInputPin());
		disarmInput.init();
		disarmInput.setDir(false);
	}
	if (!armInput.isInit()) {
		armInput.setPort(Conf::get()->armInputPort());
		armInput.setPin(Conf::get()->armInputPin());
		armInput.init();
		armInput.setDir(false);
	}
	if (!servoEnable.isInit()) {
		servoEnable.setPort(Conf::get()->servoEnbPort());
		servoEnable.setPin(Conf::get()->servoEnbPin());
		servoEnable.init();
		servoEnable.setDir(false);
	}
	K = {Conf::get()->pidKp(), Conf::get()->pidKi(), Conf::get()->pidKd()};
}

bool BoatState::insertFault (const string fault) {
	if (!this->hasFault(fault)) {
		if (this->faultCount()) faultString += ":";
		faultString += fault;
		LOG(INFO) << "Inserting fault " << fault;
	}
	return true;
}

bool BoatState::hasFault (const string fault) const {
	if (faultString.find(fault) != std::string::npos) return true;
	return false;
}

bool BoatState::removeFault (const string fault) {
	size_t index;
	index = faultString.find(fault);
	if (index != std::string::npos) {
		if (index > 0) index--;
		faultString.erase(index, fault.length() + 1);	// captures the leading colon
		LOG(INFO) << "Removing fault " << fault;
		return true;
	} else return false;
}

int BoatState::faultCount (void) const {
	if (faultString.size() == 0) return 0;	// if the string is empty, there are no faults
	int cnt = 1;							// if it's not empty, there's at least one fault here
	size_t index = faultString.find(':');	// find the first seperator (if any)
	while (index != std::string::npos) {
		cnt++;
		index = faultString.find(':', (index + 1));
	}
	return cnt;
}

bool BoatState::setBoatMode (std::string mode) {
	BoatModeEnum m;
	if (!boatModeNames.get(mode, &m)) {
		LOG(ERROR) << "Boat mode [" << mode << "] does not exist";
		return false;
	}
	_boat = m;
	return true;
}

bool BoatState::setNavMode (std::string mode) {
	NavModeEnum m;
	if (!navModeNames.get(mode, &m)) {
		LOG(ERROR) << "Navigation mode [" << mode << "] does not exist";
		return false;
	}
	_nav = m;
	return true;
}

bool BoatState::setAutoMode (std::string mode) {
	AutoModeEnum m;
	if (!autoModeNames.get(mode, &m)) {
		LOG(ERROR) << "Autonomous mode [" << mode << "] does not exist";
		return false;
	}
	_auto = m;
	return true;
}

bool BoatState::setRCmode (std::string mode) {
	RCModeEnum m;
	if (!rcModeNames.get(mode, &m)) {
		LOG(ERROR) << "RC mode [" << mode << "] does not exist";
		return false;
	}
	_rc = m;
	return true;
}

bool BoatState::isValid() {
	bool result = true;
	result &= lastFix.isValid();
	result &= launchPoint.isValid();
	result &= (health && health->isValid());
	return result;
}

Value BoatState::pack () const {
	Value d;
	int p = 0;

	p += PutVar("recordTime", HackerboatState::packTime(this->recordTime), d);
	p += PutVar("lastContact", HackerboatState::packTime(this->lastContact), d);
	p += PutVar("lastRC", HackerboatState::packTime(this->lastRC), d);
	p += PutVar("lastFix", this->lastFix.pack(), d);
	p += PutVar("launchPoint", this->launchPoint.pack(), d);
	p += PutVar("faultString", this->faultString, d);
	p += PutVar("boatMode", boatModeNames.get(this->_boat), d);
	p += PutVar("navMode", navModeNames.get(this->_nav), d);
	p += PutVar("autoMode", autoModeNames.get(this->_auto), d);
	p += PutVar("rcMode", rcModeNames.get(this->_rc), d);
	p += PutVar("disarmInput", this->disarmInput.getState(), d);
	p += PutVar("armInput", this->armInput.getState(), d);
	p += PutVar("servoEnable", this->servoEnable.getState(), d);
	try {
		if (throttle) p += PutVar("throttlePosition", throttle->getThrottle(), d);
	} catch (...) {};
	try {
		if (rudder) p += PutVar("rudderPosition", rudder->read(), d);
	} catch (...) {};
	try {
		if (relays) p += PutVar("relays", this->relays->pack(), d);
	} catch (...) {};
	if (commandCnt()) {
		Value cmdarray(kArrayType);
		for (auto &x : cmdvec) {
			cmdarray.PushBack(x->pack(), root.GetAllocator());
		}
		p += PutVar("commands", cmdarray, d);
	} else {
		p += PutVar("commands", d);
	}
	

	return d;
}

bool BoatState::parse (Value& d) {
	string time, mode;
	Value tmp;
	bool result = true;

	result &= GetVar("faultString", faultString, d);
	result &= GetVar("boatMode", mode, d);
	result &= boatModeNames.get(mode, &(this->_boat));
	result &= GetVar("navMode", mode, d);
	result &= navModeNames.get(mode, &(this->_nav));
	result &= GetVar("autoMode", mode, d);
	result &= autoModeNames.get(mode, &(this->_auto));
	result &= GetVar("rcMode", mode, d);
	result &= rcModeNames.get(mode, &(this->_rc));
	result &= GetVar("recordTime", time, d);
	result &= HackerboatState::parseTime(time, this->recordTime);
	result &= GetVar("lastContact", time, d);
	result &= HackerboatState::parseTime(time, this->lastContact);
	result &= GetVar("lastRC", time, d);
	result &= HackerboatState::parseTime(time, this->lastRC);
	result &= GetVar("lastFix", tmp, d);
	result &= this->lastFix.parse(tmp);
	result &= GetVar("launchPoint", tmp, d);
	result &= this->launchPoint.parse(tmp);

	LOG_IF(!result, ERROR) << "Parsing BoatState input failed: " << d;

	return result;
}

void BoatState::pushCmd (std::string name, const Value& args) {
	try {
		cmdvec.emplace_back(new Command(this, name, args));
	} catch (...) {
		LOG(ERROR) << "Attempted to push invalid command " << name << " with arguments " << args;
	}
	LOG(DEBUG) << "Emplacing command [" << name << "] with arguments: " << args;
}
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

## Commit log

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2014-08-03 Relocated the control board schematics
    [Hackerboat Control Board.brd, Hackerboat Control Board.sch]
2014-08-03 -- Added mechanical CAD files for steering arrangement -- Added mechanical CAD files for electronics mounting -- Added schematic for speed control relays
    [HackerBoat-Servo-Mount.FCStd, Speed Control Relays.sch, control-arm-spacer-1.FCStd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]
2014-08-03 Updated the mounting plates with new holes -- Seven relays for the relay box -- GPS shield mounting location for the control box
    [controls-mounting-plate.FCStd, relay-mounting-plate.FCStd]
2014-08-03 Adding the documentation, such as it currently exists
    [Minn Kota Endura C2-30 wiring.xlsx]
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2014-08-04 Buffer the data from the GPS UART so that we can assemble a complete NMEA sentence before parsing it. Switch to a select()-based loop instead of a polling loop. Moved the link-drop-panic code out int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
2014-08-04 Simplify parsing of $GPRMC. Fix a bug where we could block on a read from a uart if we got an EINTR in select().
2014-08-05 Further work on the state diagrams and state descriptions Added interface control document -- physical interfaces only for now
    [InterfaceControlDocument.xlsx]
2014-08-05 Still fleshing these out. Physical connections provisionally complete for InterfaceControlDocument
    [InterfaceControlDocument.xlsx]
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2014-08-06 Added state transition documents for Beaglebone and Arduino Updated state diagrams
    [HackerboatArduinoStateTransitions.xlsx, HackerboatBeagleboneStateTransitions.xlsx, InterfaceControlDocument.xlsx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]
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2014-08-07 Modified state names and descriptions per input from 3ric
    [HackerboatArduinoStateTransitions.xlsx, HackerboatBeagleboneStateTransitions.xlsx]
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2014-08-24 Updated mounting plates Updated ICD
    [InterfaceControlDocument.xlsx, controls-mounting-plate.FCStd, relay-mounting-plate.FCStd]
2014-08-25 -- Refactored code for conformance to current specs. There are too many changes for a detailed list; here's a short summary of the changes: * Reworked the state machine to encapsulate each state in i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
2014-08-30 Added a bunch of doxygen comments # Please enter the commit message for your changes. Lines starting # with '#' will be ignored, and an empty message aborts the commit. # On branch master # Changes t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
2014-08-30 -- Implemented almost all core functions -- TODO: Determine which messages to use -- TODO: Implement NVM -- Added some MAVLink messages we will probably need -- Updated state transitions # Please ent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
    [HackerboatArduinoStateTransitions.xlsx, HackerboatBeagleboneStateTransitions.xlsx]
2014-09-03 Added hardware test code Various modifications to 'as-built' condition Added TODO.md
    [Hackerboat Control Board.brd, Hackerboat Control Board.sch, HackerboatArduinoStateTransitions.xlsx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]
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2015-06-30 adding gps module, slight modifications made to fix errors (does not currently work)
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2015-08-09 Not sure when I made these changes...
    [InterfaceControlDocument.xlsx]
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2015-09-06 mapping Beaglebone message fields to Beaglebone states
    [HackerboatArduinoStateTransitions.xlsx]
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2015-09-07 Excel decided to save these, not sure why
    [HackerboatArduinoStateTransitions.xlsx, SensorOffsetCalculator.xlsx]
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2015-09-12 fixed uart/udp determination bug
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2015-09-24 Fixed issue with lastState that was causing sensor fault on self-test
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2015-09-24 Set horn timer to two seconds to prevent homicidal rage
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2015-09-24 Fixed timeouts for buttons, made lights static variables so they work correctly
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2015-09-25 Added some more feedback, fixed a stupid steering bug, and cleaned up some indenting.
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2015-09-26 Trying again on fixing steering pickup code
2015-09-26 Trying again on fixing steering pickup code, take whatever
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2015-09-26 Added line to write the steering error correctly
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2015-09-26 Added continuous printouts for the compass calibration and a test program for seeing if it works correctly.
2015-09-27 Compass fixes -- make sure to re-calibrate every operational day until further notice.
    [2015Sep26-1410-mag-data.csv]
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2015-11-22 Documents for the restful refactoring
    [Arduino REST.xlsx, Arduino States.xlsx, Beaglebone REST.xlsx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]
2015-11-22 restored a couple of files I should not have deleted
    [InterfaceControlDocument.xlsx, SensorOffsetCalculator.xlsx]
2015-11-29 Documentation updates for refactoring
    [Arduino REST.xlsx, Arduino States.xlsx]
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2015-12-11 Writing up the Beaglebone state transitions and bringing main systems doc up to speed.
    [Beaglebone States.xlsx]
2015-12-29 Added new dumpState function to the Arduino
    [Arduino REST.xlsx]
2016-01-03 Reworked the beaglebone REST code with saner dispatch etc. Still could use some more decomposition, but coming along.
    [Beaglebone REST.xlsx]
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2016-02-04 Update TODO.md
    Holy shit it's been a long time since I updated this. Marked stuff that's done done. Software portion needs a top to bottom re-write in light of current issue list.
2016-02-07 Finished writing implementation of the RESTDispatch classes
    [Beaglebone REST.xlsx]
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2016-02-22 More work on getting the state machine coded up
    [Beaglebone States.xlsx]
2016-03-01 Found a minor error, corrected it
    [hackerboatMasterControl.cpp]
2016-03-05 Finished implementing the state machine states
    [Beaglebone States.xlsx]
2016-03-07 Finished writing the parse/pack routines
    [Arduino REST.xlsx]
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2016-03-12 Broke out arduinoStateClass into its own source file and implemented all specific methods. Implemented file open and close for error logging in logs.cpp and added time stamping. Made small modificati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
    [RESTdispatch.cpp]
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2016-03-17 Updated Arduino REST to include break up of dumpState function
    [Arduino REST.xlsx]
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2016-03-18 Some additional unit tests for trivial object<->JSON roundtripping, and their corresponding bug fix.
    [RESTdispatch.cpp]
2016-03-19 Updated Arduino communication to use the JSON return values correctly
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2016-03-20 Added a simple JSON roundtrip test for the Arduino state class. Fixed a couple bugs in its pack/parse methods; also wrote some utilities to make parse/pack methods easier to write and converted it to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
2016-03-24 A bunch of missing semicolons. Some state/mode terminology changes to match the changes in bone/arduino classes. Moved some RESTdispatch constructors out-of-line.
    [RESTdispatch.cpp, hackerboatMasterControl.cpp]
2016-03-31 Some more compilation fixes.
    [config.h]
2016-03-31 More master control compilation
    [Beaglebone States.xlsx]
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2016-04-10 Fixing compilation of targetWaypoint
    [config.h]
2016-04-11 Found the problem with frame time calculations
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2016-04-12 Changed timing on master control and navigation daemons to use nanosleep rather that signals
    added a using declaration...
    more compilation fixit
    more compilation fixit
    more compilation fixit
    more compilation fixit
    more compilation fixit
    Added timing diagnostic pic to nav loop.
    Removing redundant state timer class
    Changed timing on master control and navigation daemons to use nanosleep rather that signals
    more compilation fixit
    more compilation fixit
    more compilation fixit
    more compilation fixit
    [hackerboatMasterControl.cpp]
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2016-04-12 Fixing nav so that we don't have to suck in the waypoint
    Fixing compilation of targetWaypoint
    Compilation fixit
    Compilation fixit
    Fixing compilation of targetWaypoint
    Compilation fixit
    Compilation fixit
    [config.h]
2016-04-12 Found the problem with frame time calculations
    Tinkering with the time calculations...
2016-04-13 Changed various instances of writeRecord() to appendRecord(). Improved .gitignore. Fixed arduinoStateClass initialization.
    [config.h, hackerboatMasterControl.cpp]
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2016-04-18 Fixed up various warnings...
    [RESTdispatch.cpp]
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2016-04-25 Fixed outbound serial speed for Arduino connection
2016-05-01 Futzing around with serial problems...
    [config.h]
2016-05-02 Changes to improve speed and stability of REST connection to the Arduino
    [hackerboatMasterControl.cpp]
2016-05-07 Fix a printf format specifier.
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2016-06-25 A bunch of serial fixes
    [config.h]
2016-06-25 Working on fixing the initialization stuff
    [RESTdispatch.cpp]
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2016-07-05 Fixed build errors resulting from recent commits.
    [RESTdispatch.cpp]
2016-07-06 Working on getting the DB writing working correctly for these...
    [hackerboatMasterControl.cpp]
2016-07-10 Various fixes to make the master control process read correctly from the Arduino.
    [config.h, hackerboatMasterControl.cpp]
2016-07-16 Finally fixed the DB conflicts.
    [RESTdispatch.cpp, hackerboatMasterControl.cpp]
2016-07-16 Initial trimming of unnecessary parts in preparation for serious work. Keeping the power supply circuits, BBB connection, IMU, and GPS.
    [Hackerboat Control Board.brd, Hackerboat Control Board.sch]
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2016-07-16 Added a couple of things missed to the diagram.
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2016-07-21 Everything in except the 15V boost converter and a couple of connectors
    [Hackerboat Control Board.brd, Hackerboat Control Board.sch]
2016-07-23 All placed and routed for the control board.
    [Hackerboat Control Board.brd, Hackerboat Control Board.sch]
2016-07-24 Fixed conditionals in REST code.
    [RESTdispatch.cpp]
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2016-07-26 Fixing the DRC
    [MotorController.brd]
2016-07-27 Changed the R/C input over to SBUS. Updates to the PowerDistributionBaord
    [Hackerboat Control Board.brd, Hackerboat Control Board.sch, PowerDistributionBoard.brd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]
2016-07-30 Making sure we have the latest board in github
    [Hackerboat Control Board.brd, Hackerboat Control Board.sch, MotorController.brd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]
2016-07-31 Added mode and dataflow diagrams. Updated board schematic and layout with comments from hardware review.
    [Hackerboat Control Board.brd, Hackerboat Control Board.sch]
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2016-08-05 Created first panel for the power distribution & control boards. Needed to rename some things to make them work with gerbmerge.
    [HackerboatControlBoard.brd, HackerboatControlBoard.sch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]
2016-08-06 Final gerbers, score file removed, plus first attempt at documentation for software for this hardware.
    [control-power-distro-panel.cfg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]
2016-08-06 Created a mechanical drawing for building a case.
    [HackerboatControlBoard.brd]
2016-08-09 Deleted some old documentation, renamed some, and stared documentation of the communications process.
    [Arduino REST.xlsx, Arduino States.xlsx, Beaglebone REST.xlsx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]
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2016-08-26 It all compiles! ais.cpp is a work in progress... and now requires C++14 b/c being able to write 600s and have the compiler correctly interpret that as at time period of 600 seconds is kind of awesom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
    [ais.hpp, config.h, hackerboatMasterControl.cpp]
2016-08-28 Fixed some issues with .gitignore and added some values and attributes to the power distribution board
    [PowerDistributionBoard.brd, PowerDistributionBoard.sch]
2016-08-29 Finished implementing ais.cpp. Found some potential memory leaks in gps.cpp, patched them.
    [ais.hpp]
2016-08-31 Pulled over the PID library from Arduino and fixed up the time pack/parse routines so they compile. NOTE: This required switching over to g++-6 as the compilation environment. This took a little bit 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
2016-09-06 Added an Excel file documenting my pin mapping findings for the PWM subsystem. Made some minor changes to make the schematic more readable.
    [HackerboatControlBoard.sch, pwm-mapping.xlsx]
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2016-09-19 -- Changed raw values in ADC so they come out as ints -- Entered a good value for the battery_mon path in config.h -- Deleted some old stuff from config.h -- Modified names for rudder servo pins in c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
    [adc128d818.cpp, adcInput.cpp, boatState.cpp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]
2016-09-22 Switched out the i2c drivers for lsquaredc library in lsm303 driver. This appears to actually do the correct repeated start incantation to get the chip to work. I don't think I'm setting the correct 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
    [config.h, lsm303.cpp]
2016-09-22 The raw sensor read now works! Hell of a time getting the conversion from two bytes to a 16-bit two's complement value working correctly.
    [lsm303.cpp]
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2016-09-24 -- Removed i2c module (replaced with lsquaredc) -- Created relay_test.cpp -- Fixed relay.{hpp|cpp} module so it works now
    [adc128d818.cpp, config.h, gpio.cpp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]
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2016-09-27 -- Modified config.h with the correct relay arrangement -- Modified config.h with the correct magnetometer calibration values -- Made the compass work, with help from a Cypress appnote
    [config.h]
2016-09-29 Fixed ADC subsystem so it works now.
    [adc128d818.cpp, adcInput.cpp, config.h]
2016-10-02 Completed PID unit test, along with a couple of code fixes to make it pass.
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2016-11-25 Autonomous tests mostly done -- just need to finish up the anchor mode tests. TODO: write mqtt tests TODO: fix the bloody logging
    [boatState.cpp]
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2017-01-21 Bunch of stuff to fix things after re-imaging.
    [boatModes.cpp, boatState.cpp, gpio.cpp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]
2017-01-22 Master control now compiles and runs without obvious problems.
    [boatState.cpp, relay.cpp]
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2017-02-07 Fixed Command class so that the argument JSON is properly decref'd.
    [boatState.cpp]
2017-03-30 Adafruit.IO REST interface up and running smoothly. A number of minor issues squashed. Currently smashes the stack on arm badly enough to crash GDB.
    [adc128d818.cpp, config.h]
2017-04-02 Fixed up all uses of delete to also set the value of the deleted pointer to NULL using the new REMOVE() macro
    [boatModes.cpp, hackerboatMasterControl.cpp, navModes.cpp]
2017-04-08 Some memory fixes. Added a waypoint publishing routine. Added a GPS averaging routine.
    [boatState.cpp, config.h]
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2017-04-15 -- Added command line singleton to util.{hpp|cpp} -- Modified logging and printing of waypoints to work correctly -- Modified logging and printing of the current waypoint to handle return & anchor ca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
    [ais.hpp, boatModes.cpp]
2017-04-23 Fixed rudder test so that it works
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2017-06-10 Fixed the rudder and magnetic deviation issues for test on 11Jun2017
    [configuration.cpp]
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2017-06-17 Fixed missing voltage/current information in logs. Fixed missing declination.
    [adcInput.cpp, boatState.cpp, hackerboatMasterControl.cpp]

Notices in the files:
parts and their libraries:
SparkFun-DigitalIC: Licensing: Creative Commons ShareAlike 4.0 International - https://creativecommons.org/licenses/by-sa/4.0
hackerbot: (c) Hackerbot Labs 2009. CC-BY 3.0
